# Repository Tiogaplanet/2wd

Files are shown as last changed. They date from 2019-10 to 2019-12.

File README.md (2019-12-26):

# 2wd

The two-wheeled robot with a low center of gravity.

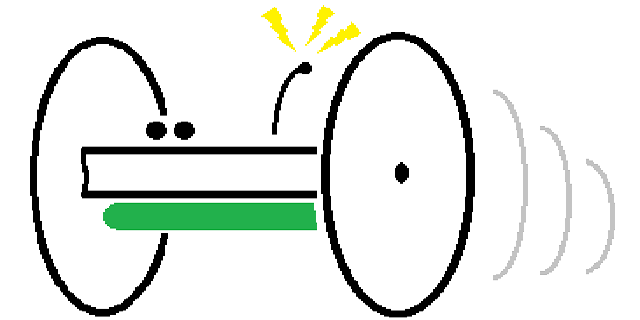
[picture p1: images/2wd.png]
A high-quality, professional artist's conceptual rendering of 2wd.


**This repository contains the Eagle files for 2wd and a running log of its development.**

I like [MiP](https://github.com/Tiogaplanet/MiP_ESP8266_Library).  There's no denying the mobile inverted pendulum, for which it gets its name, is an innovative design.  Unfortunately the innovation comes at the cost of increased battery consumption.  MiP cannot come to a resting position as long as it is powered on.  In order to remain upright it must constantly rebalance itself to prevent from toppling over.

Other consumer grade robots such as Anki's [Vector](https://anki.com/en-us/vector.html) or [Cozmo](https://anki.com/en-us/cozmo.html) use a tracked design.  The many four-wheeled Arduino kits for sale around the Internet use skid steering similar to Vector and Cozmo at the cost of decreased agility compared to MiP's differential steering.  I'm looking for a different approach that has the agility of MiP but without the skid steering or complexity of a tracked or four-wheel drive system.

My solution is a robot with two parallel wheels, side by side, a layout known as a dicycle.  Technically, MiP fits this definition however I picture a design with the center of gravity below the horizontal center line of the wheels.  Such a design would conserve battery power when the robot is at rest.

I have found only a couple notable examples of such a design online.  [Parrot's Sumo](https://www.parrot.com/us/minidrones/parrot-jumping-sumo) fits the description but it appears to be dragging a solid tail to counter torque and keep the robot upright.  The best example I've seen of a self-balancing dicycle comes from [Simon Winder](http://simonwinder.com/2015/06/two-wheeled-rolling-robot/).  Winder's robot uses an inertial measurement unit (IMU) to keep the body upright and it uses infrared to avoid obstacles.

I propose developing a robot similar to Winder's, built around the Arduino Nano 33 IoT, which has an integrated six-degree IMU along with WiFi and Bluetooth.  The robot will also include an on-board battery management system, IR detection, an OLED display and eventually a camera.

I'll update the bill of materials for prototyping as I develop the robot.  For now it looks like this:

| Description | Quantity |
|---|---|
| [Arduino Nano 33 IoT](https://store.arduino.cc/usa/nano-33-iot) | 1 |
| 15 pin female headers for Nano | 2 |
| [90x10mm wheels](https://www.pololu.com/product/1435) | 2 |
| [Gear motors](https://www.pololu.com/product/1520) | 2 |
| [Gear motor bracket pair](https://www.pololu.com/product/2681) | 1 |
| [Magnetic encoder pair](https://www.pololu.com/product/1523) | 1 |
| [Motor driver](https://www.pololu.com/product/2135) | 1 |
| 7 pin female headers for driver | 2 |
| [IR sensors](https://www.pololu.com/product/2476) | 2 |
| [Battery management system (BMS)](https://www.amazon.com/gp/product/B07S7PKPH6/ref=ppx_yo_dt_b_asin_title_o03_s00?ie=UTF8&psc=1) | 1 |
| [Prototype board (7x9 cm) for motherboard and drive/power board](https://www.amazon.com/gp/product/B072Z7Y19F/ref=ppx_yo_dt_b_asin_title_o04_s01?ie=UTF8&psc=1) | 2 |
| 18650 batteries | 2 |
| [Voltage regulator](https://www.amazon.com/gp/product/B00IJYDJTS/ref=ppx_yo_dt_b_search_asin_title?ie=UTF8&psc=1) | 1 |
| 15mm PCB stand-offs, nuts and screws for regulator | 2 |
| [DC barrel jack](https://www.amazon.com/gp/product/B074LK7G86/ref=ppx_yo_dt_b_asin_title_o04_s00?ie=UTF8&psc=1) | 1 |
| [SPDT switch](https://www.ebay.com/itm/12-Breadboard-slide-switches-3-pin-50-volt-500-milliamp-SPDT-switch-Arduino/112891316956) | 1 |
| 26mm PCB stand-offs, nuts and screws for motherboard and drive/power board | 4 |
| [OLED display](https://www.amazon.com/gp/product/B072Q2X2LL/ref=ppx_yo_dt_b_search_asin_title?ie=UTF8&psc=1) | 1 |
| PCB stand-offs, nuts and screws for OLED display | 4 |

## 24 December 2019

I spent today finishing the power circuit and moving the motor controller and Nano onto the chassis.  I set the voltage regulator module output to 5.1 volts.  That will provide enough juice to power both motors.  The voltage regulator onboard the Nano (VIN) will get it down to the 3.3 volts required by the Nano 33 IoT.  

This first picture shows the voltage regulator module connected to the BMS.  I used a simple jumper as an on/off switch to conserve space on the board while I ponder a better solution.  The output of the voltage regulator is connected to the prototype board so that I can pass power to the top board where the Nano and motor controller are soldered.

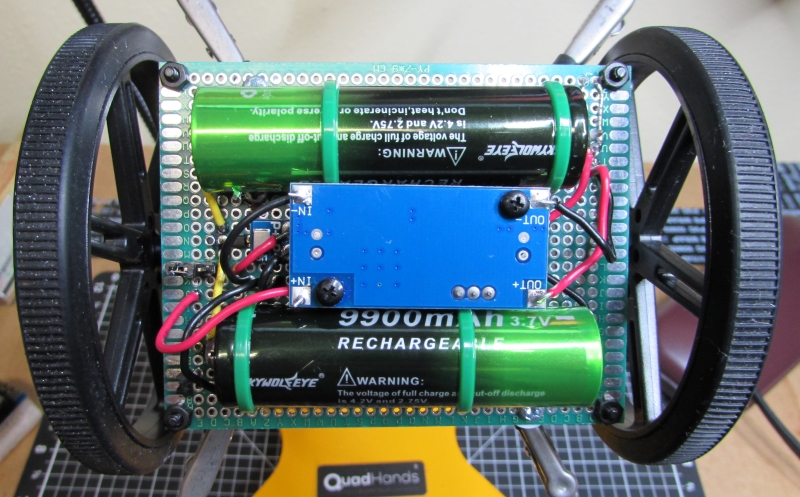
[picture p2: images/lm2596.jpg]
The voltage regulator module is connected to the BMS.


After some debugging in software I got the thing working.  I found that my check for an established serial connection would cause the entire sketch to hang when the robot was finally untethered from the computer.

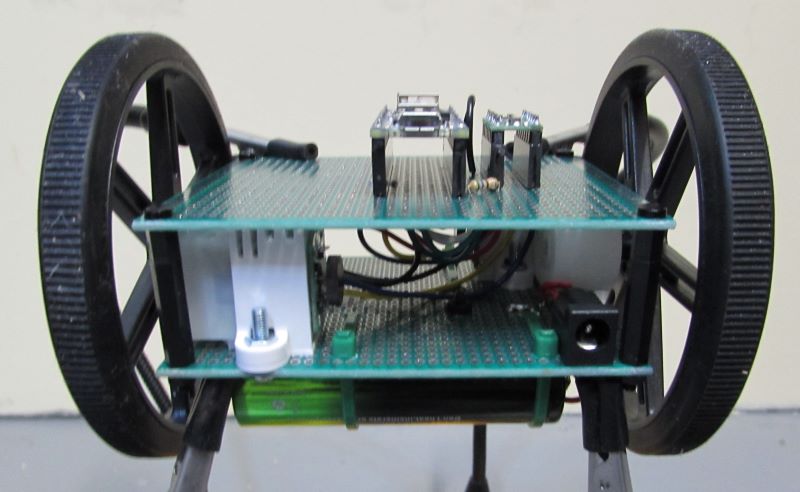
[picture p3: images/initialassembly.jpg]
Motors, motor controller, Nano and power are installed on the chassis.


Next steps are to implement PID in the library to keep the body level while moving and get the IR sensors working.

## 21 December 2019

Spent a few hours tonight soldering up the batteries, BMS and barrel jack.  The picture below shows  everything together.

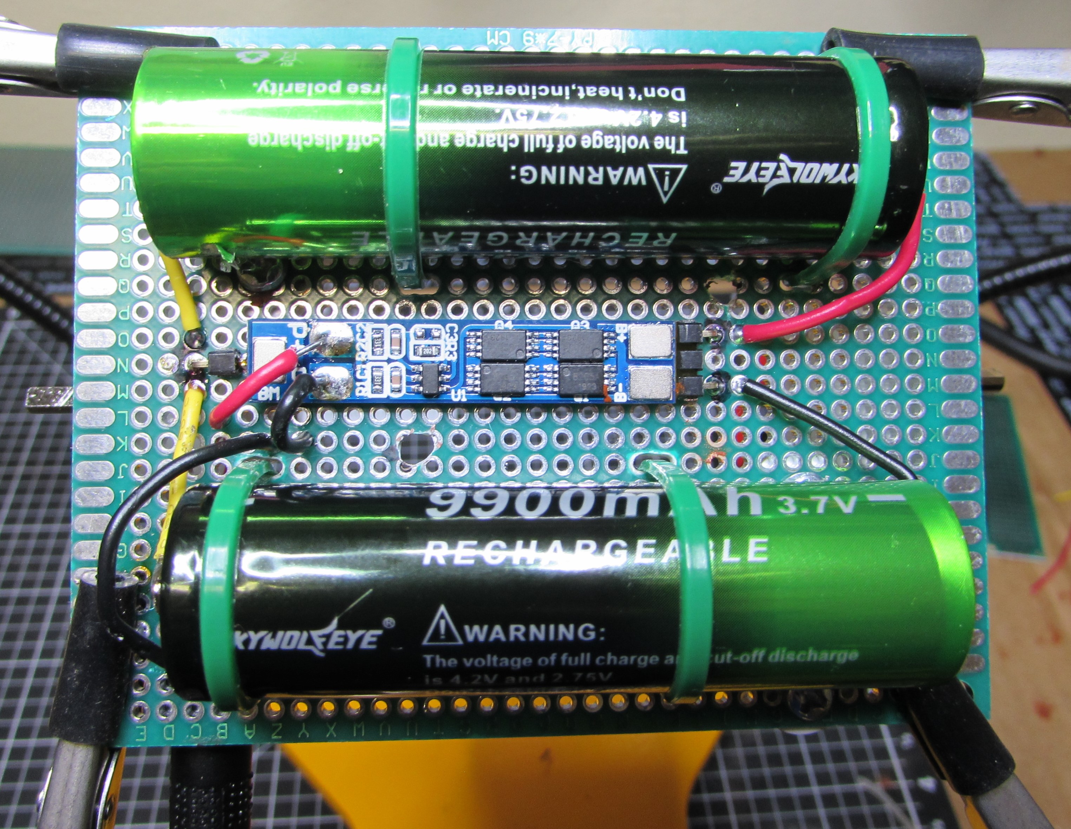
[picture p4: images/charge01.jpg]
The charging circuit is connected.


The next picture shows a test fit of the voltage regulator.  I am holding off on installing the voltage regulator until I decide what kind of power switch to use.  The motors have a peak draw of 1.2 amps.  Because of that I'm debating a plain old SPDT switch or a MOSFET-based switch circuit.

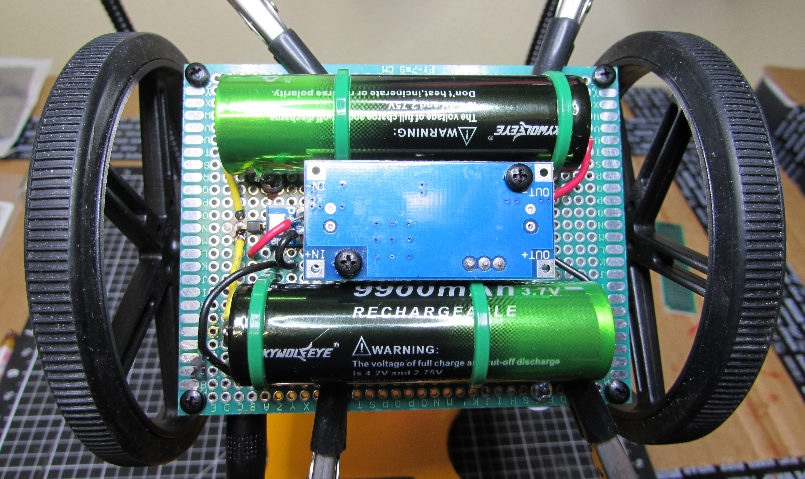
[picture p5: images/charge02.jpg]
The voltage regulator is shown in a test fit between the two batteries and below the BMS.


I was concerned that this robot would be made up of too many modular circuits like the voltage regulator, but seeing how nicely it fits made me glad I decided to use it instead of assembling my own regulator circuit from scratch.

## 19 December 2019

No new work.  Just sharing some of my latest pictures.  Below is a picture of 2wd doing some bench testing.  It's sitting on the box for the Nano 33 IoT while I test code for operating the motors.  I'm using the Arduino Uno clone behind the breadboard to power the motors.  The motors still need more current than what the Uno clone provides.  However, I have received some 2.1mm DC barrel jacks in the mail so I will be able to connect a wall-wart power supply to the motors via the LM2596 module.

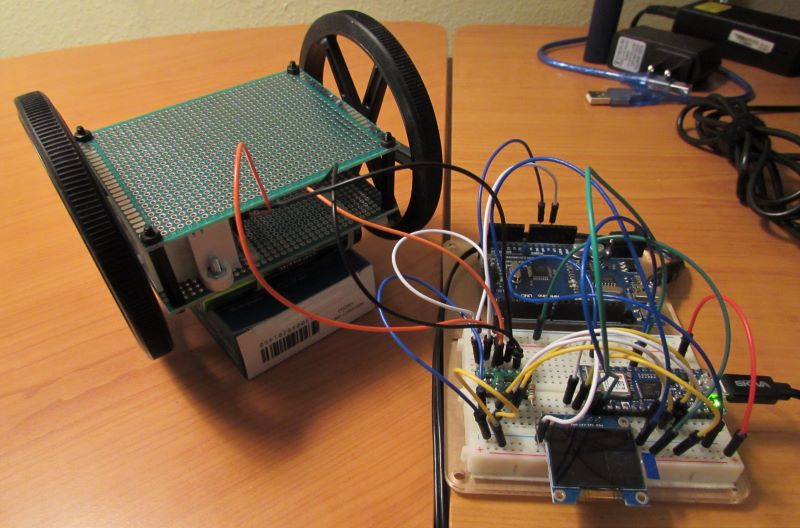
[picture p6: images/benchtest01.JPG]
2wd is bench tested. Here it is sitting on the box for the Nano 33 IoT so that the motors can spin freely while undergoing test.


I soldered a few right-angle pins onto the BMS to make it fit onto the prototyping board that makes up 2wd's chassis.  I didn't use a lot of solder in case I needed to undo it.  Once everything tests out I'll do come back and re-solder the right-angle pins.

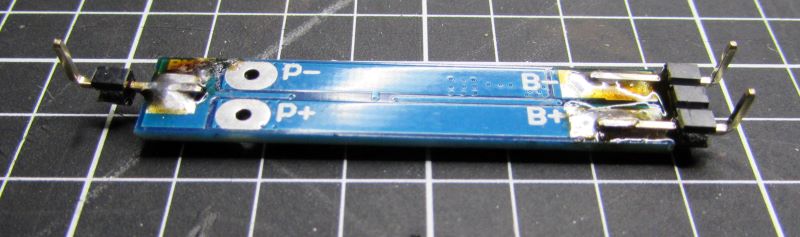
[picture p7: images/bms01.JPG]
A view of the underside of the battery management system shwoing right angle pins to make the BMS prototyping- and breadboard-friendly.


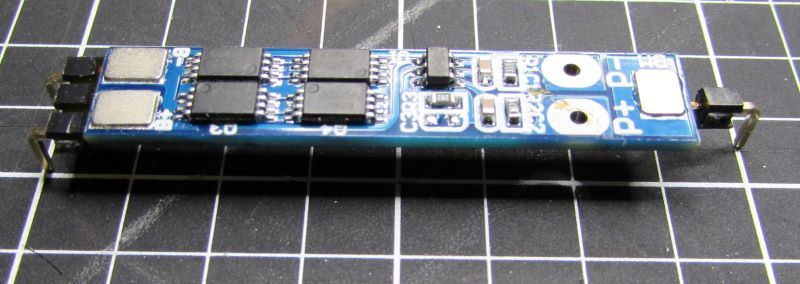
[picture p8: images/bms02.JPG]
A view of the top of the battery management system.


The LM2596 module doesn't plug into a prototyping board either but it has screw holes so I plan to drill holes in the prototyping board and mount the module using PCB stand-offs.

## 13 December 2019

The last several weeks I have tried organizing a place to work in my latest home.  Today I was finally able to assemble a few things.

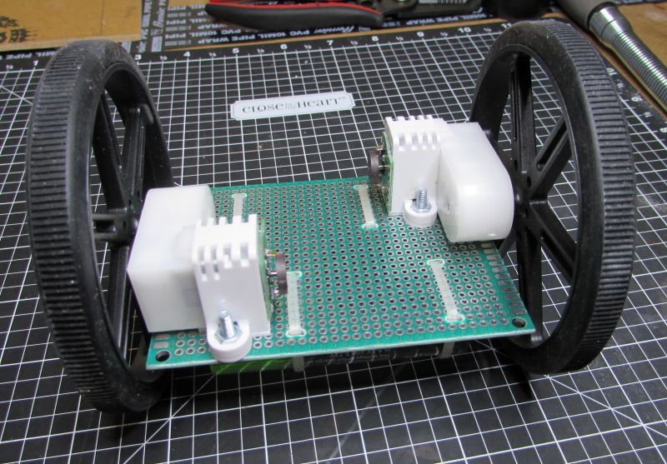
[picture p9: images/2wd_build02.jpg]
A view of the top side of 2wd. Motors and batteries are assembled on opposite sides of the center line to balance weight.


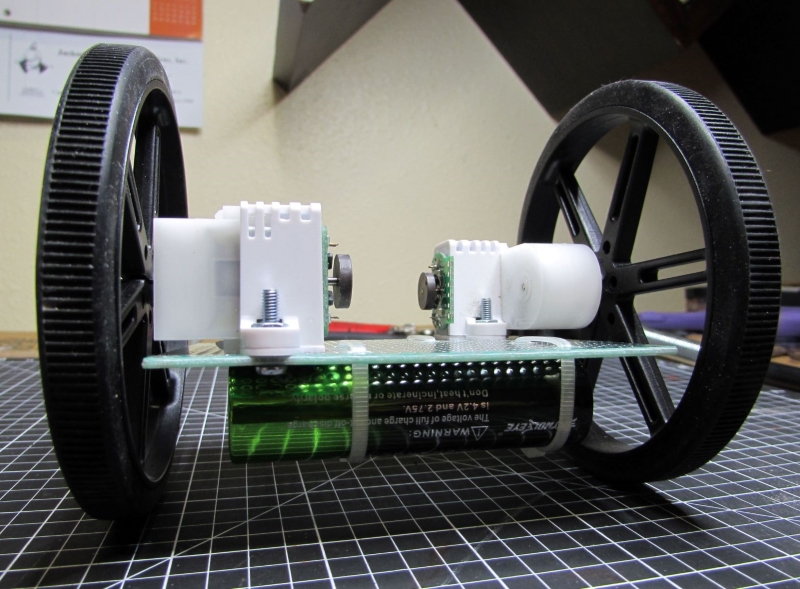
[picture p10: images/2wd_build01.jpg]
A view of the front of 2wd. The batteries are mounted near the front and rear edge of the main prototyping board.


Not shown in the pictures above is a "motherboard" mounted above the gear motors using PCB stand-offs in the pre-drilled holes of the prototyping board.  I realized quickly that I did not have enough space to mount the Nano, OLED display and pretty much anything else after securing the gear motors and batteries to the drive/power board.  While this will make the body of the robot taller, it will still be within the diameter of the wheels and won't come close to offsetting the weight of the batteries.  It should also reduce body flex between the two wheels.

I have breadboard-tested the motor driver using pulse-width modulation in a simple sketch.  The wheels turn forward together at a medium speed before momentarily stopping, then turning backward.  In the same sketch I also tested the use of an OLED display.  So far, so good.  Although, I still need to develop an [actual library](https://github.com/Tiogaplanet/2wd_library) to drive the robot.

Next, I plan to sort out the power and charging system.  I have soldered right-angle pins to the BMS to make it "breadboard friendly."  It will sit close to the prototype board so for now I plan to install it underneath the robot, between the batteries with the voltage regulator stacked below it using PCB stand-offs. Now I'm just waiting for the barrel jack and power switch to arrive in the mail before I assemble anything else.

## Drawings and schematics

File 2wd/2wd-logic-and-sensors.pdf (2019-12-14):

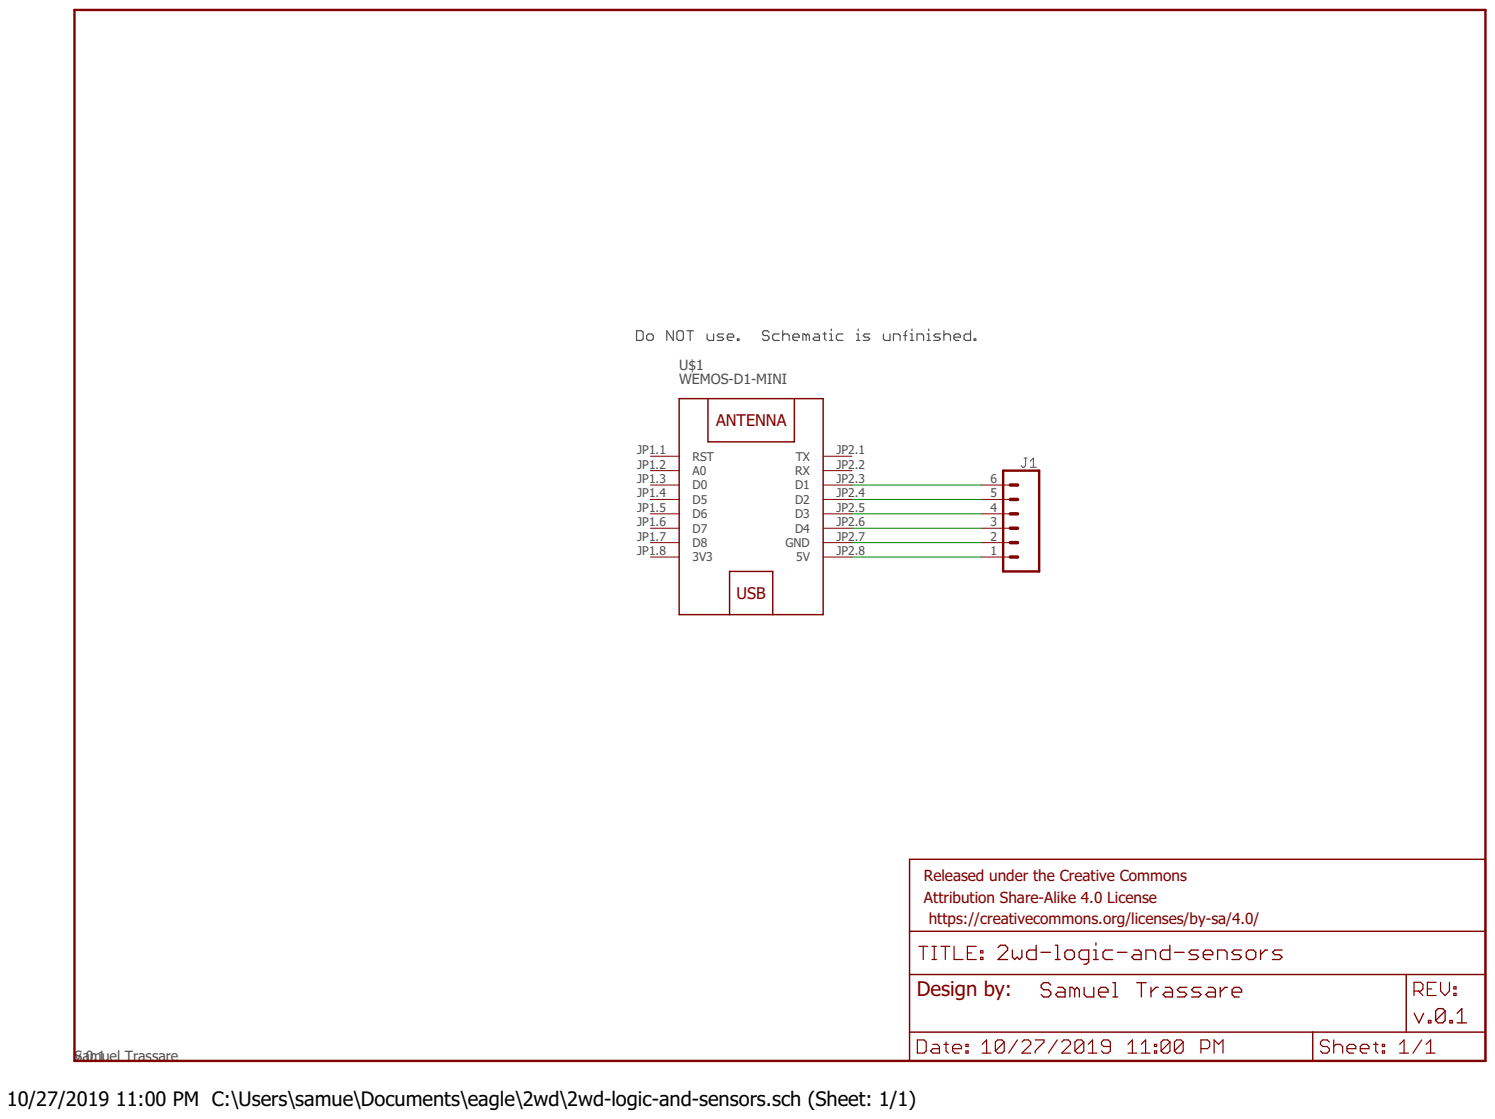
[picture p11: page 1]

Released under the Creative Commons Attribution Share-Alike 4.0 License https://creativecommons.org/licenses/by-sa/4.0/

10/27/2019 11:00 PM C:\Users\samue\Documents\eagle\2wd\2wd-logic-and-sensors.sch (Sheet: 1/1)

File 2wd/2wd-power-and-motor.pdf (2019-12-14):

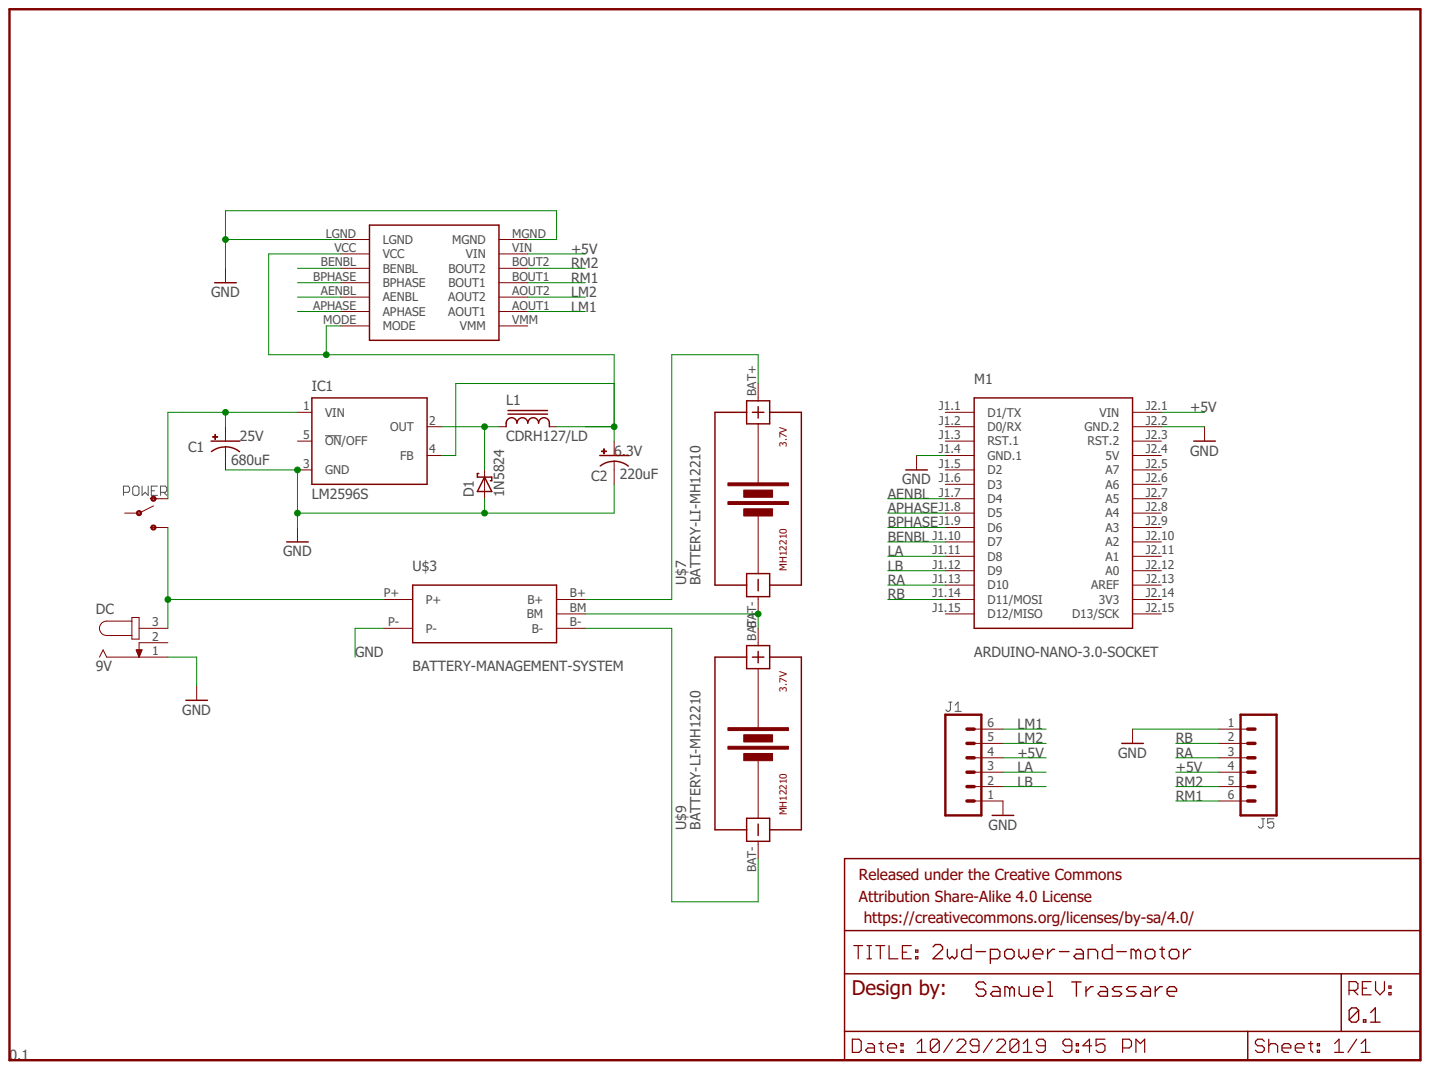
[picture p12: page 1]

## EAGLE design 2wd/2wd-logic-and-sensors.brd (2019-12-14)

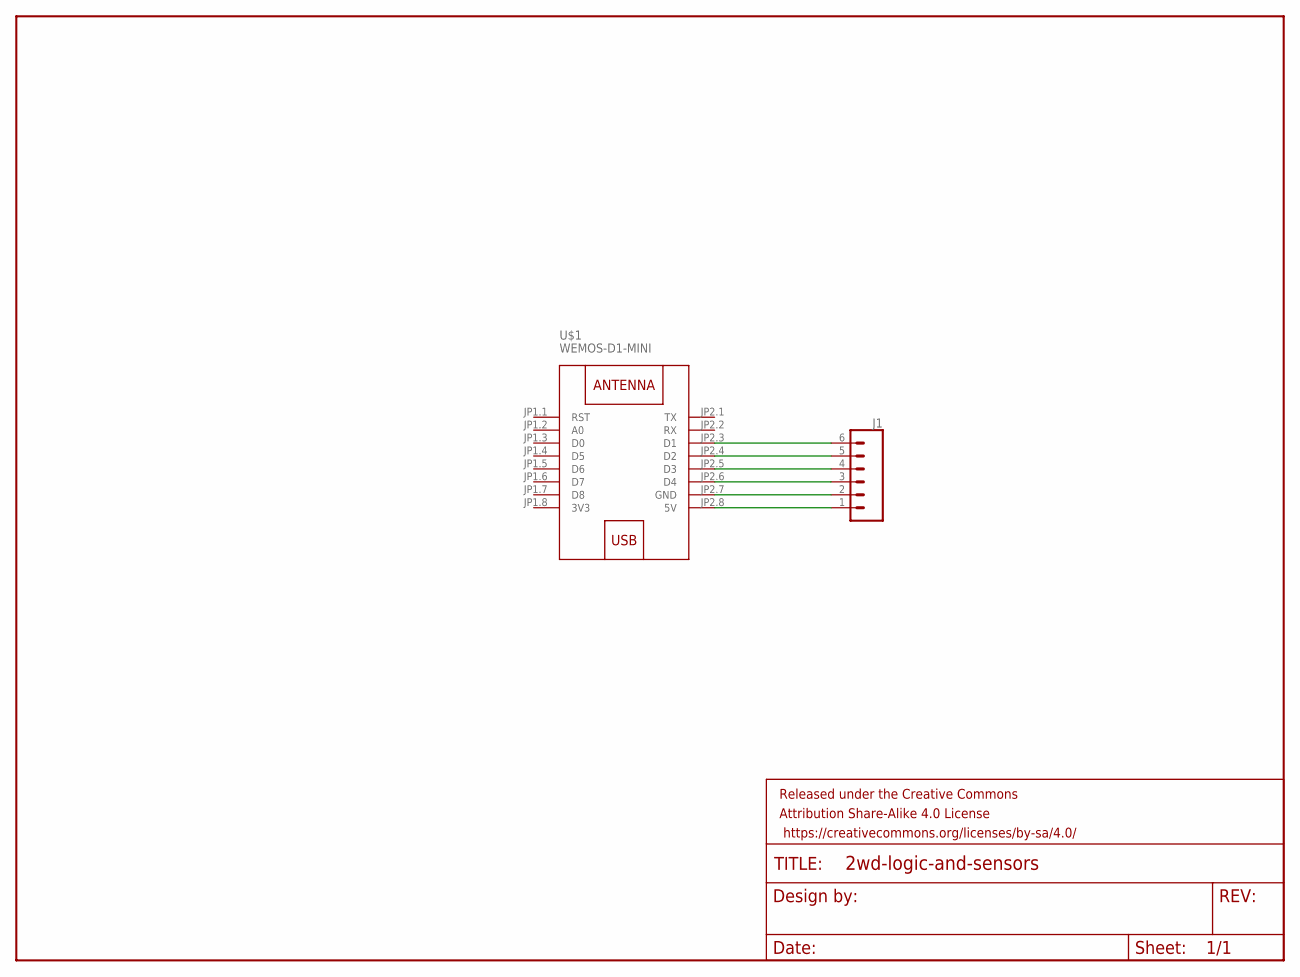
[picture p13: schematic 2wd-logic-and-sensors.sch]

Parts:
FRAME1: FRAME-LETTER; CREATIVE_COMMONS
J1: CONN_06NO_SILK_FEMALE_PTH; 1X06_NO_SILK
U$1: WEMOS-D1-MINI

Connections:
3V3: U$1.JP1.8 (3V3)
unnamed: J1.1, U$1.JP2.8 (5V)
unnamed: J1.2, U$1.JP2.7 (GND)
unnamed: J1.3, U$1.JP2.6 (D4)
unnamed: J1.4, U$1.JP2.5 (D3)
unnamed: J1.5, U$1.JP2.4 (D2)
unnamed: J1.6, U$1.JP2.3 (D1)

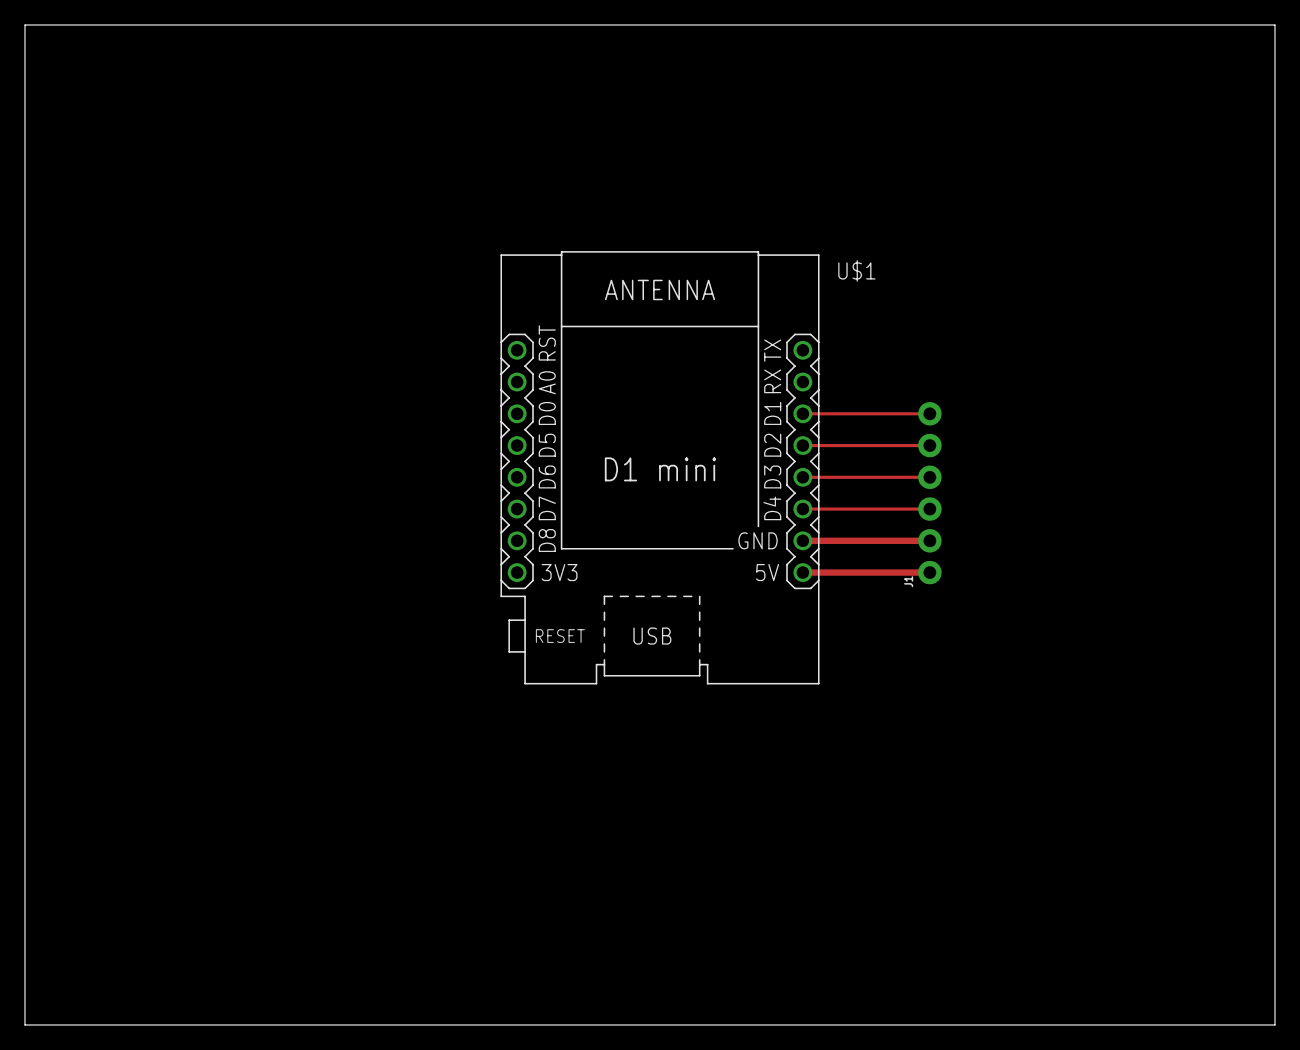
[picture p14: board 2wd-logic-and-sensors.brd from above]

Board: 2 copper layers, 100.0 x 80.0 mm, 3 parts (0 on the bottom side), 6 nets.

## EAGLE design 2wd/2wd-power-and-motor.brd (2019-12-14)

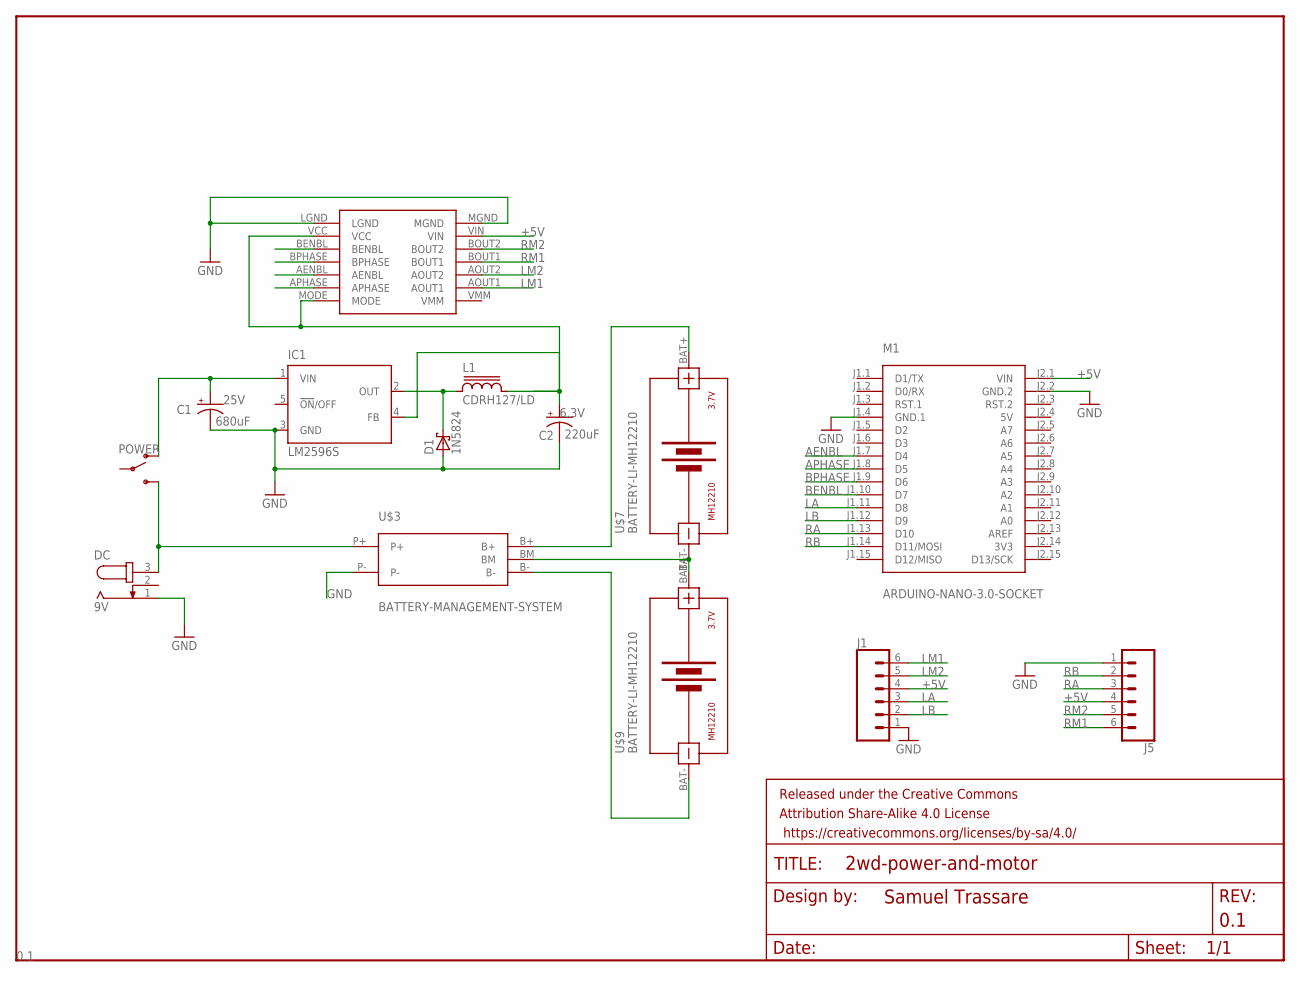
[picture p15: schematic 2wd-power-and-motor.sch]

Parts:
C1: 680uF; E5-10,5; VOLTAGE 25V
C2: 220uF; UD-6,3X5,8_NICHICON; VOLTAGE 6.3V
D1: 1N5824; SMB
DC: 9V; SPC4077
FRAME1: FRAME-LETTER; CREATIVE_COMMONS
IC1: LM2596S; TO263-5
J1: CONN_06LEFT_MOTOR_CONN; LEFT_MOTOR_CONN
J5: CONN_06RIGHT_MOTOR_CONN; RIGHT_MOTOR_CONN
L1: CDRH127/LD
M1: ARDUINO-NANO-3.0-SOCKET
POWER: SWITCH-SPDT-PTH-11.6X4.0MM; SWITCH_SPDT_PTH_11.6X4.0MM
U$2: POLOLU_MOTOR_DRV8835THROUGHHOLE; POLOLU_MOTOR_DRV_DRV8835
U$3: BATTERY-MANAGEMENT-SYSTEM
U$7, U$9: BATTERY-LI-MH12210

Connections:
3V3: M1.J2.14 (3V3)
5V: M1.J2.4 (5V)
+5V: J1.4, J5.4, M1.J2.1 (VIN), U$2.VIN
AENBL: M1.J1.7 (D4), U$2.AENBL
APHASE: M1.J1.8 (D5), U$2.APHASE
BENBL: M1.J1.10 (D7), U$2.BENBL
BPHASE: M1.J1.9 (D6), U$2.BPHASE
FB: C2.+, IC1.4 (FB), L1.2
GND: C1.-, C2.-, D1.A, DC.1, IC1.3 (GND), J1.1, J5.1, M1.J1.4 (GND.1), M1.J2.2 (GND.2), U$2.LGND, U$2.MGND, U$3.P-
LA: J1.3, M1.J1.11 (D8)
LB: J1.2, M1.J1.12 (D9)
LM1: J1.6, U$2.AOUT1
LM2: J1.5, U$2.AOUT2
unnamed: DC.3, POWER.3 (S), U$3.P+
unnamed: U$3.B+, U$7.BAT+
unnamed: U$3.B-, U$9.BAT-
unnamed: U$3.BM, U$7.BAT-, U$9.BAT+
unnamed: U$2.MODE, U$2.VCC
OUT: D1.C, IC1.2 (OUT), L1.1
RA: J5.3, M1.J1.13 (D10)
RB: J5.2, M1.J1.14 (D11/MOSI)
RM1: J5.6, U$2.BOUT1
RM2: J5.5, U$2.BOUT2
VIN1: C1.+, IC1.1 (VIN)

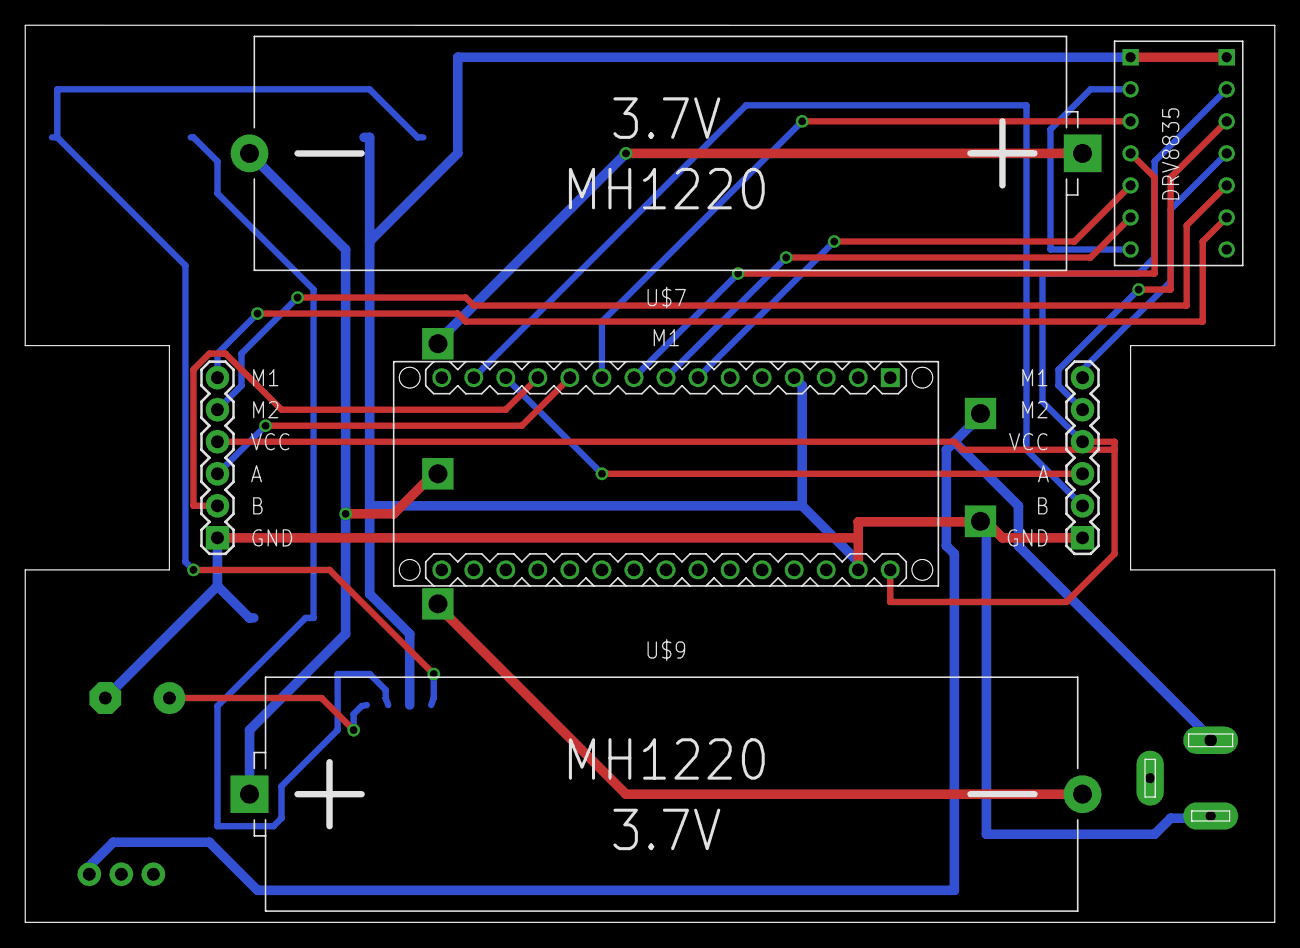
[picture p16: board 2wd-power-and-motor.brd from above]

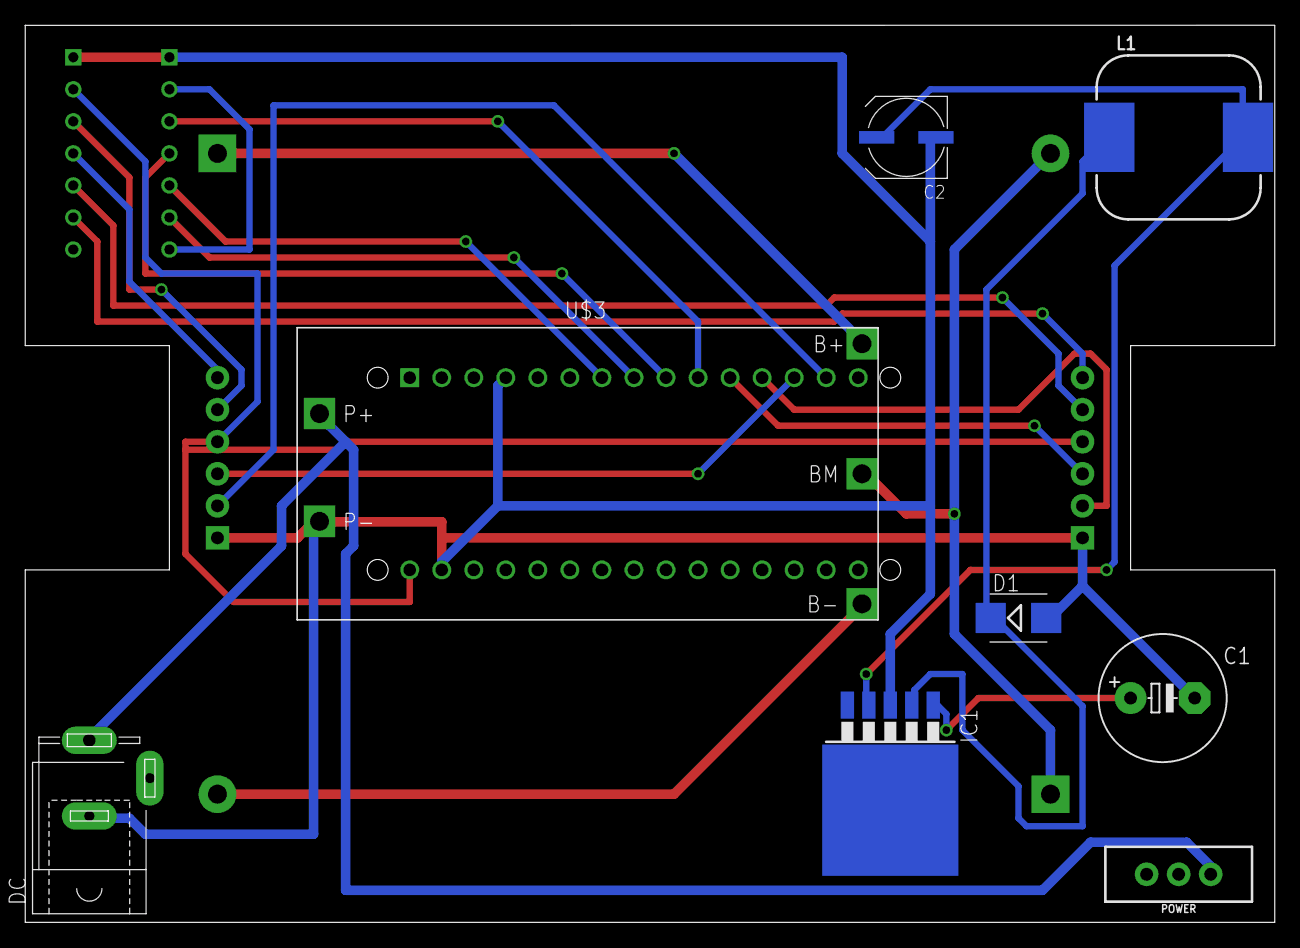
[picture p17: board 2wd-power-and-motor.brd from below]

Board: 2 copper layers, 99.1 x 71.1 mm, 15 parts (8 on the bottom side), 22 nets.

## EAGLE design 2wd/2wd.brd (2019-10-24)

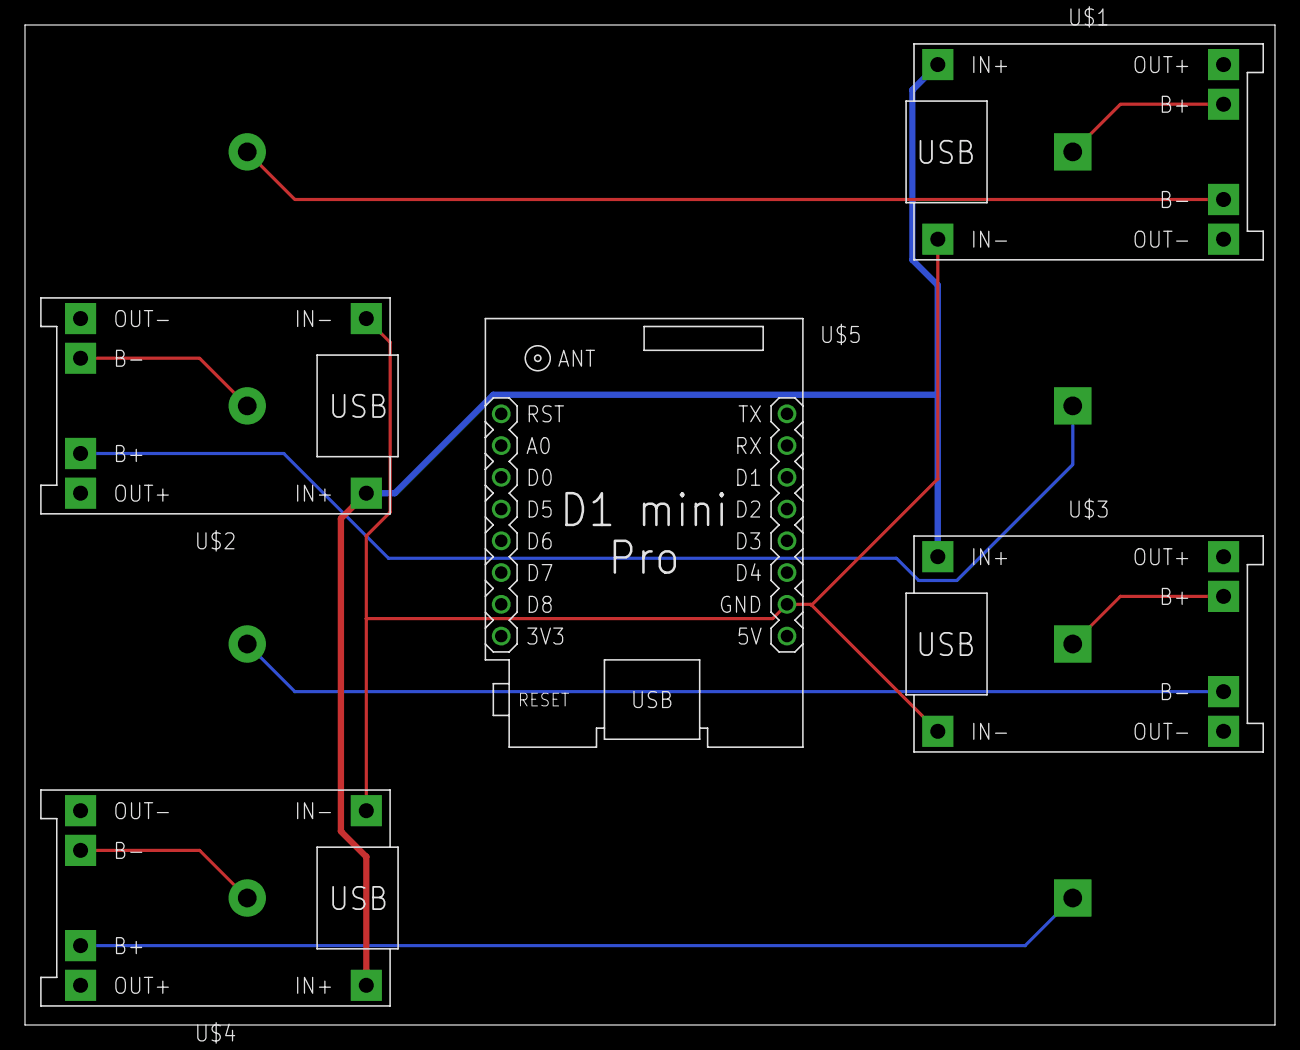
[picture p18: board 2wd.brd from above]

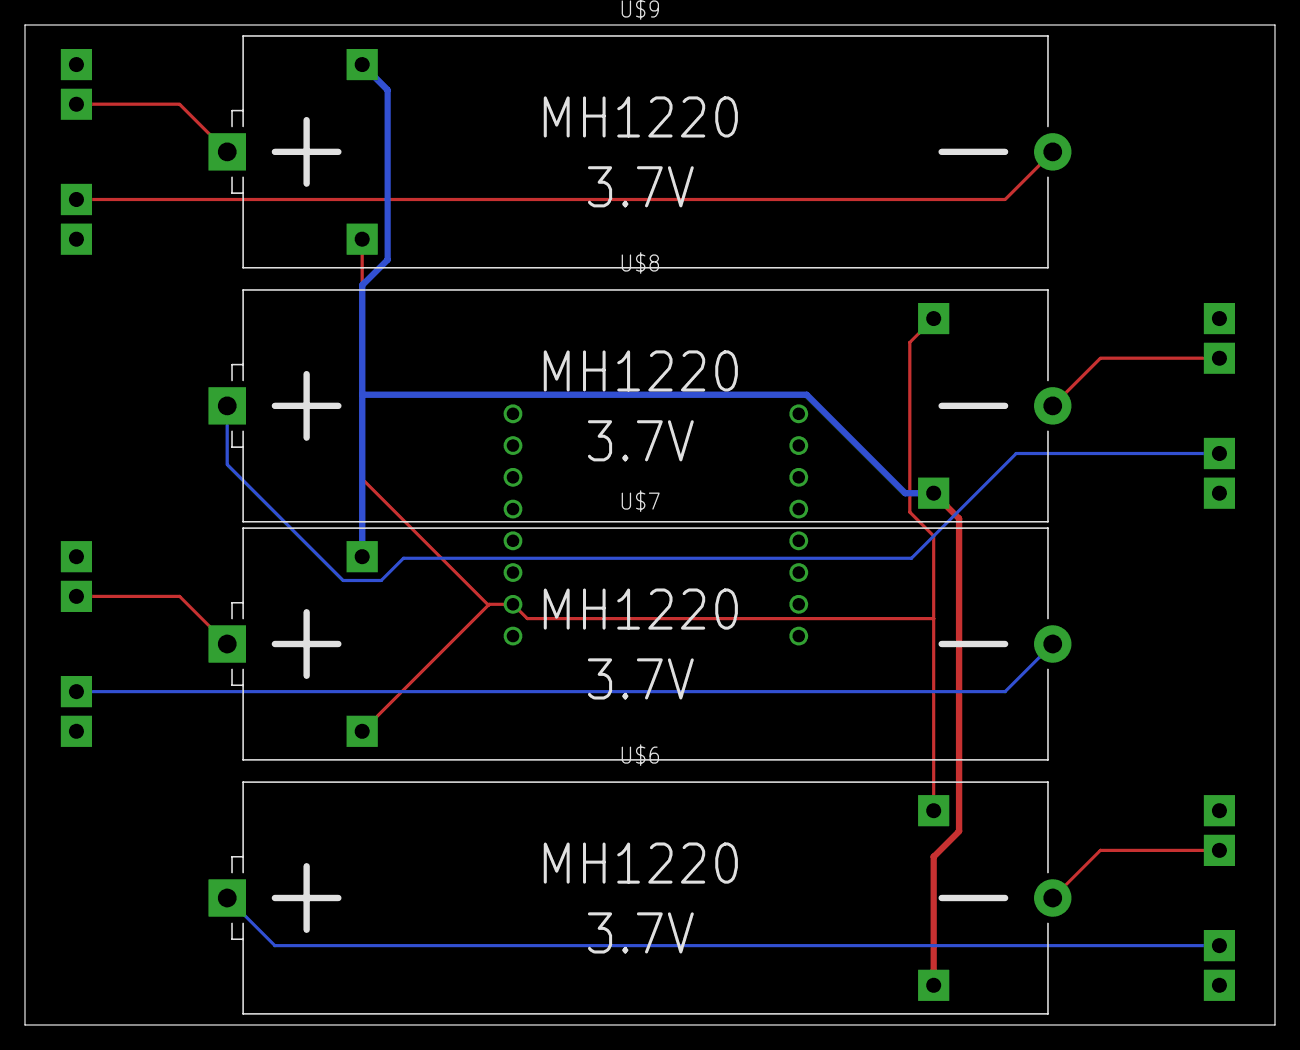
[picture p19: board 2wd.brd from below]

Board: 2 copper layers, 100.0 x 80.0 mm, 10 parts (4 on the bottom side), 10 nets.

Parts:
FRAME1: FRAME-LETTER; CREATIVE_COMMONS
U$1, U$2, U$3, U$4: BATTERY-CHARGER-LI-PROT
U$5: WEMOS-D1-MINI-PRO
U$6, U$7, U$8, U$9: BATTERY-LI-MH12210

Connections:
GND: U$1.IN-, U$2.IN-, U$3.IN-, U$4.IN-, U$5.JP2.7
unnamed: U$1.B-, U$9.BAT-
unnamed: U$2.B-, U$8.BAT-
unnamed: U$3.B-, U$7.BAT-
unnamed: U$4.B-, U$6.BAT-
unnamed: U$3.B+, U$7.BAT+
unnamed: U$2.B+, U$8.BAT+
unnamed: U$1.B+, U$9.BAT+
unnamed: U$4.B+, U$6.BAT+
VCC: U$1.IN+, U$2.IN+, U$3.IN+, U$4.IN+

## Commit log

2019-10-24 Initial eagle files
    [2wd.brd, 2wd.sch]
2019-10-24 Start adding power control
    [2wd.brd, 2wd.sch]
2019-10-28 Created two boards in Eagle.
    Finally decided to create two boards within one Eagle project. A motherboard and a power management/motor controller daughterboard.
    [2wd-logic-and-sensors.brd, 2wd-logic-and-sensors.sch, 2wd-power-and-motor.brd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]
2019-10-29 Resized board, added motor driver.
    [2wd-power-and-motor.brd, 2wd-power-and-motor.sch]
2019-10-30 Added integrated voltage regulation
    [2wd-power-and-motor.brd, 2wd-power-and-motor.sch]
2019-12-17 Expound upon the diary entry, clarify the readme.
    Original update was short because I didn't have a lot of type to write a good, thorough entry. I've come back and expounded upon the weekend's work and update the BOM and my way ahead.
2019-12-22 Charging circuit

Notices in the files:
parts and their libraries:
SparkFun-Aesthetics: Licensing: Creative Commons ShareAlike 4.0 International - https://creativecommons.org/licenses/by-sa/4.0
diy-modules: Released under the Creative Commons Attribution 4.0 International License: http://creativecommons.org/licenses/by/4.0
